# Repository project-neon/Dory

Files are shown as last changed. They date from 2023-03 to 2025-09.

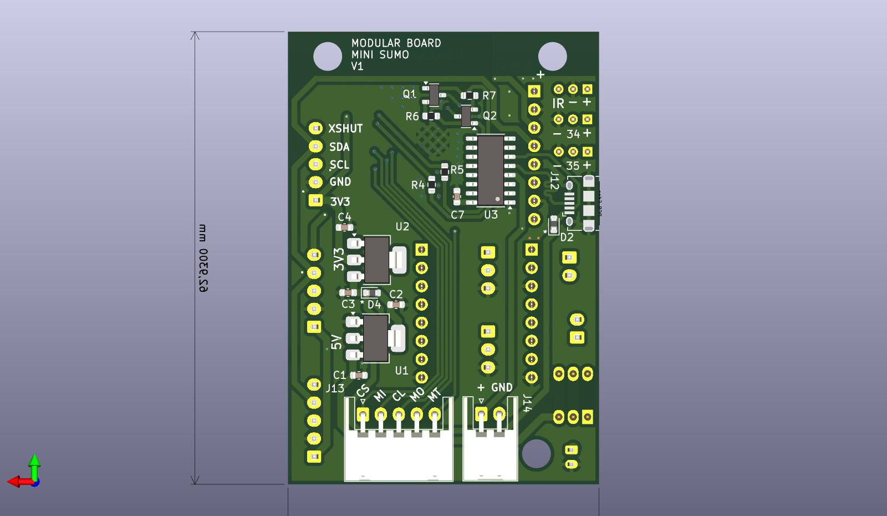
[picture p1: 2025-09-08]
Electronics/Arquivos do projeto/Sumo_Geral_Modular B.jpg

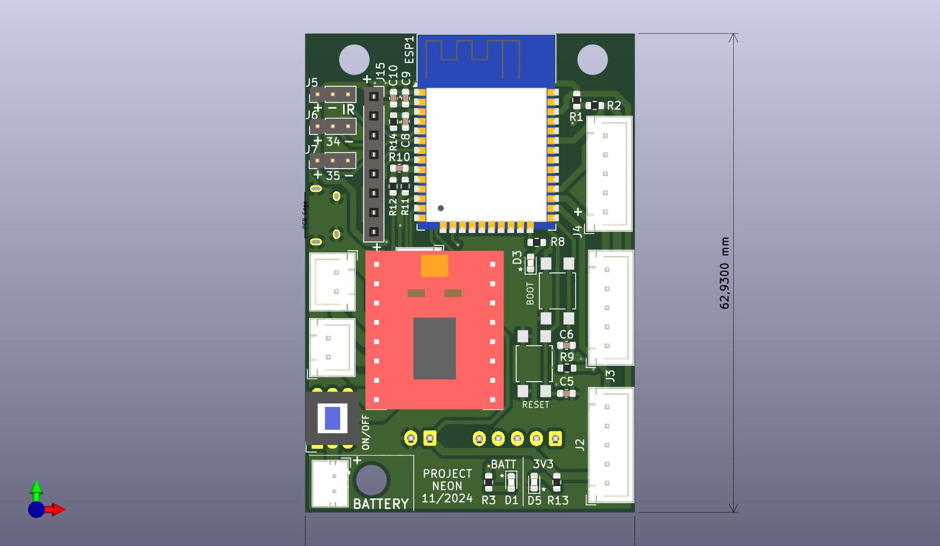
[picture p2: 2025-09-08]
Electronics/Arquivos do projeto/Sumo_Geral_Modular F.jpg

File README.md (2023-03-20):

# Dory
3rd Sumo Robot for Project Neon. After Zumo and Nemo, comes Dory.

Repositório de desenvolvimento para a Dory em 2022.

Usamos o fluxo de trabalho apresentado [aqui pelo Gamen](https://github.com/project-neon/codestyleguide/blob/master/git.md). Também está apresentado no [github flow](https://docs.github.com/pt/get-started/quickstart/github-flow). O resumo seria este:

## Arquivos

  Neste repositório temos os principais arquivos que usamos para os 3 capítulos, Eletrônica, Mecânica e Software. Segue abaixo uma lista do que temos em cada uma das pastas:

  ### Electronics
    Na parte eletrônica, utilizamos o programa Kicad que é open source e permite a criação e edição de PCBs.
    Caso queira editar ou vizualizar o projeto, clone o diretório "Eletronics", pois nele está contido o esquemático 
    no formato PDF e sch,  a PCB no formato pcb e os arquivos pro e plr próprios do Kicad.
    
  ### Mechanics
    Na pasta da mecânica, há arquivos no formato step e stl para que possam ser utilizados para visualização 
    e manufatura 3D, juntamente com os arquivos pdf dos desenhos técnicos para melhor compreensão do projeto
    
  ### Software
    Nesta pasta deixamos todos os arquivos que formam o código do robô. Então .ino e .h são os principais arquivos.
    Usamos os .h's para segmentar o código e não ser um único bloco enorme, dividindo eles de acordo com sua funcionalidade.
    O .ino é onde fica a base de todo o código, como o setup() e o loop(). Temos os códigos de testes e o código autonomous
    que usamos durante as lutas oficiais.

## Fluxo Git
- Quando for acrescentar uma feature (um comportamento novo para o robô), crie uma brancha chamada `feat/nome-da-feature`
- Quando for corrir algum bug no código, crie uma brancha chamada `fix/nome-do-fix`
- Quando for adicionar novos arquivos na mecância ou eletrônica, crie uma brancha chamada `update/eletronics-<data>` ou `update/mechanis-<data>`, exemplo: `update/eletronics-01-04-2023`
- A partir da main: `git checkout -b nome-da-branch`, ex: `git checkout -b feat/novos-testes`

## Na hora de fazer o commit
- Nomeie o seu commit primeiro dizendo o que foi feito, ex: `fix: `, `feat: ` ou `update: `
- Você pode adicionar no assunto (comentário) ou na mensagem do commit também onde que a mudança foi feita.
- `git push`

Para saber mais de commits, você pode acessar esse [link](https://www.freecodecamp.org/news/how-to-write-better-git-commit-messages/)

## Na hora de fazer o merge
- Depois de subir o commit, crie um PR (Pull Request) e peça pro resto do pessoal da equipe dar uma conferida antes de ser aprovado



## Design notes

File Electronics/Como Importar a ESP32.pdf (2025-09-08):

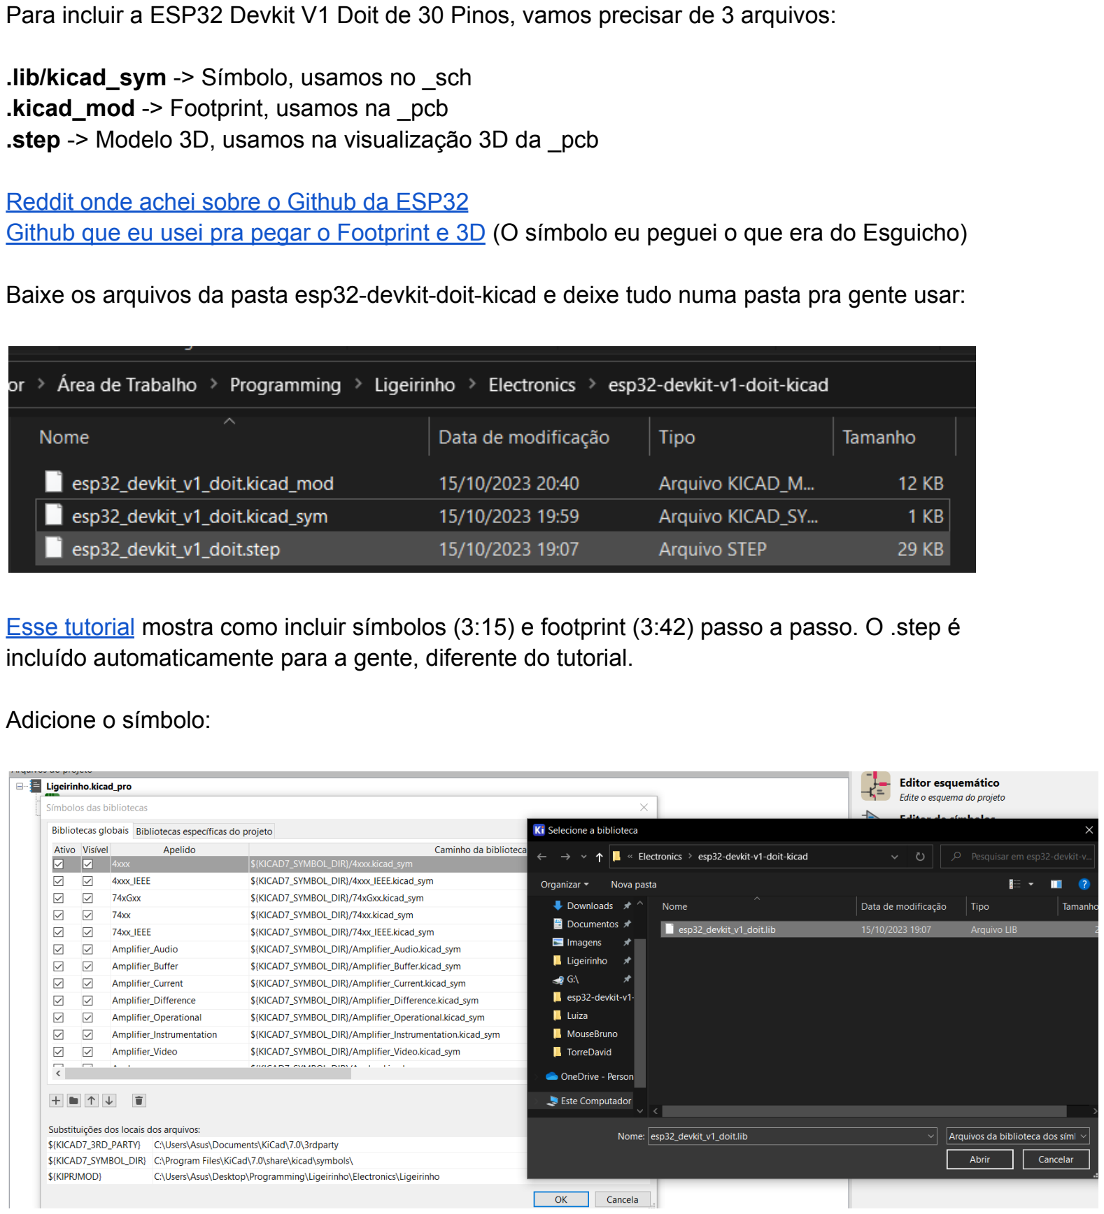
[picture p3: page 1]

Para incluir a ESP32 Devkit V1 Doit de 30 Pinos, vamos precisar de 3 arquivos:

.lib/kicad_sym -> Símbolo, usamos no _sch
.kicad_mod -> Footprint, usamos na _pcb
.step -> Modelo 3D, usamos na visualização 3D da _pcb

Reddit onde achei sobre o Github da ESP32 (https://www.reddit.com/r/esp32/comments/hufwwl/looking_for_kicad_symbolfootprint_for_esp_doit/)
Github que eu usei pra pegar o Footprint e 3D (https://gitlab.com/VictorLamoine/kicad/-/tree/master?ref_type=heads) (O símbolo eu peguei o que era do Esguicho)

Baixe os arquivos da pasta esp32-devkit-doit-kicad e deixe tudo numa pasta pra gente usar:

Esse tutorial (https://www.youtube.com/watch?v=W9cLnIjvybo&ab_channel=PlumPot) mostra como incluir símbolos (3:15) e footprint (3:42) passo a passo. O .step é incluído automaticamente para a gente, diferente do tutorial.

Adicione o símbolo:

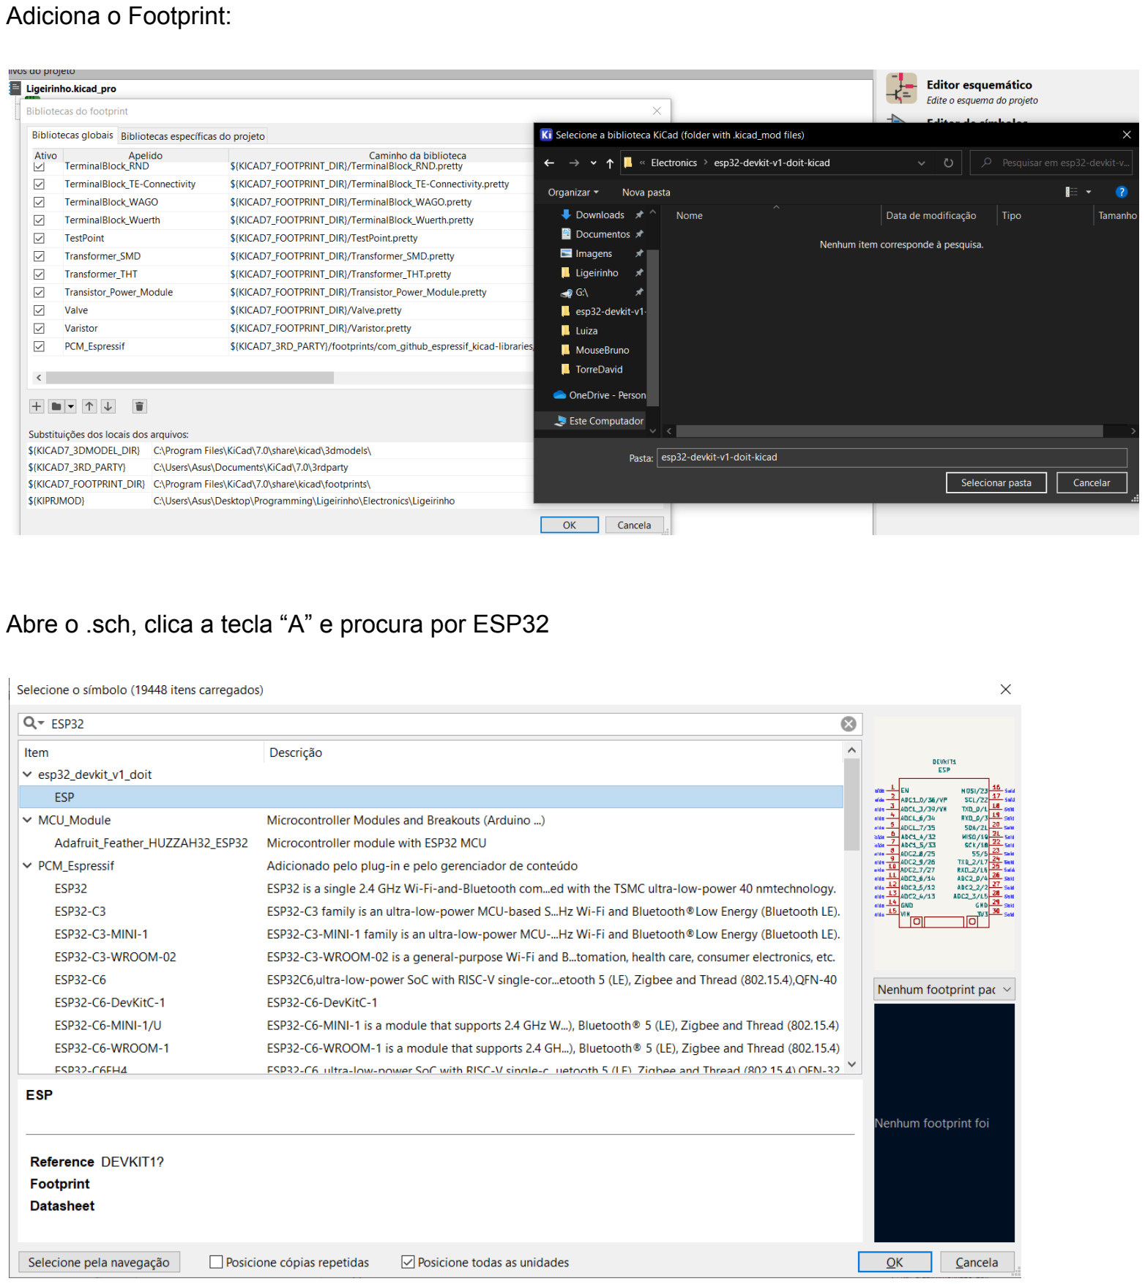
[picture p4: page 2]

Adiciona o Footprint:

Abre o .sch, clica a tecla “A” e procura por ESP32

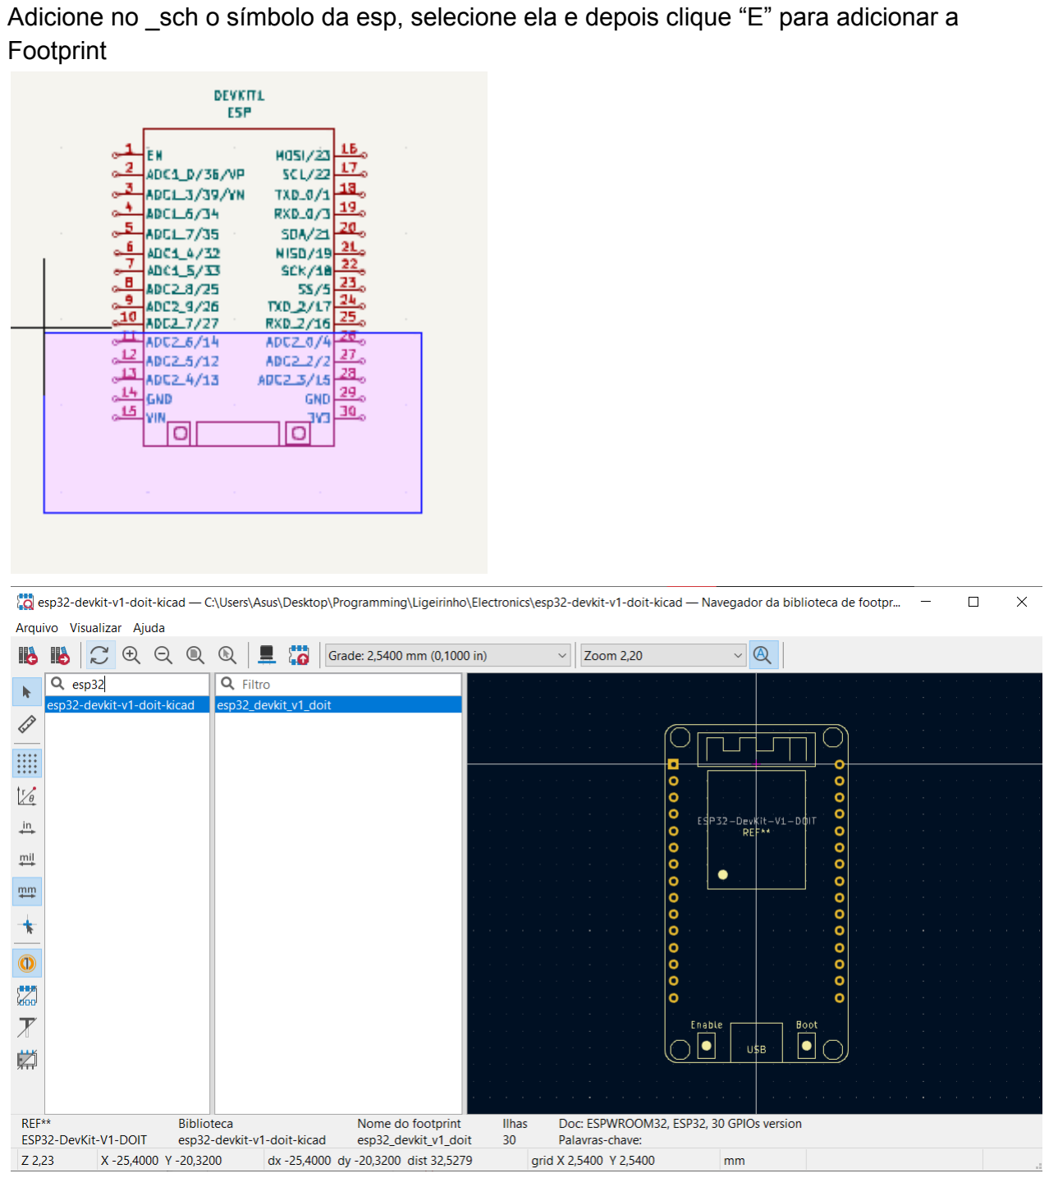
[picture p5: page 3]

A

dicio

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
p, s

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
cliq

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
dicio

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
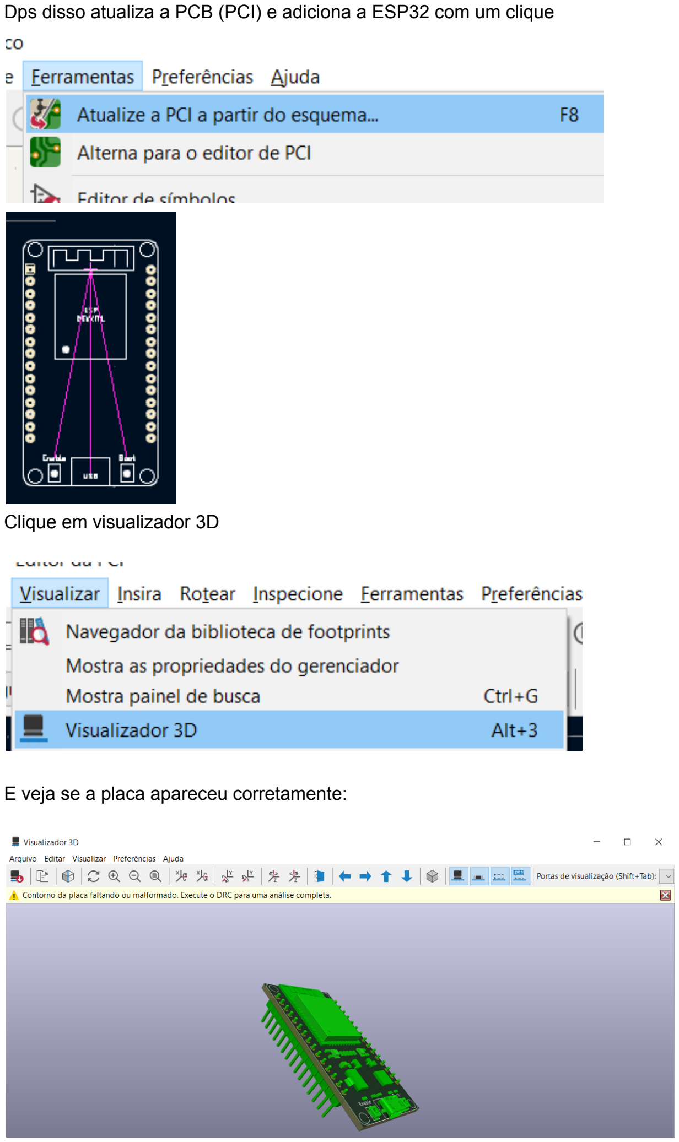
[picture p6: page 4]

Dps disso atualiza a PCB (PCI) e adiciona a ESP32 com um clique

Clique em visualizador 3D

E veja se a placa apareceu corretamente:

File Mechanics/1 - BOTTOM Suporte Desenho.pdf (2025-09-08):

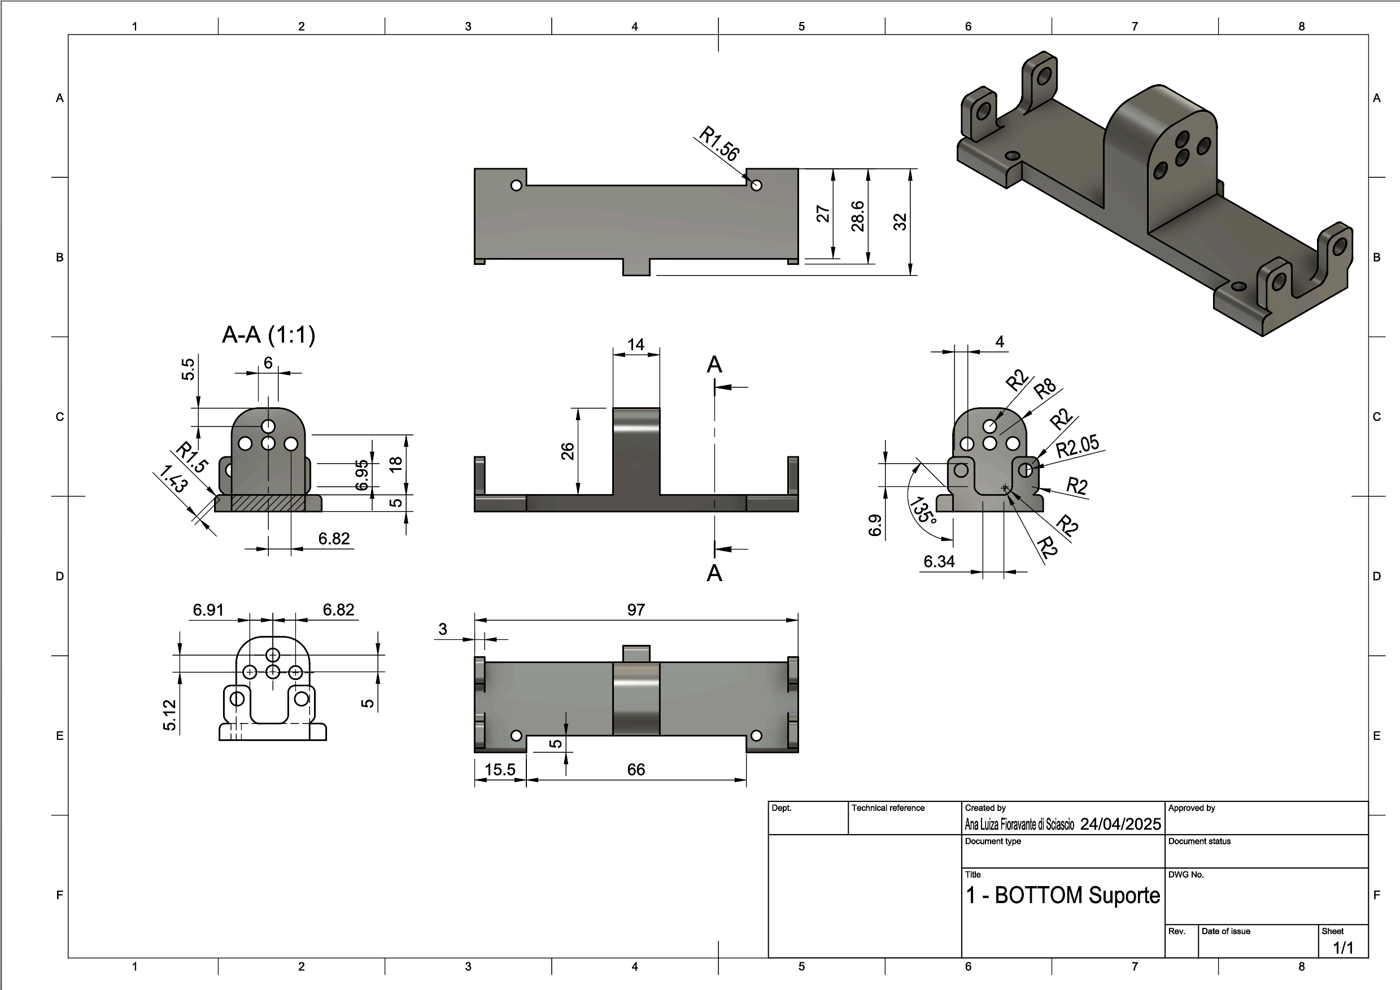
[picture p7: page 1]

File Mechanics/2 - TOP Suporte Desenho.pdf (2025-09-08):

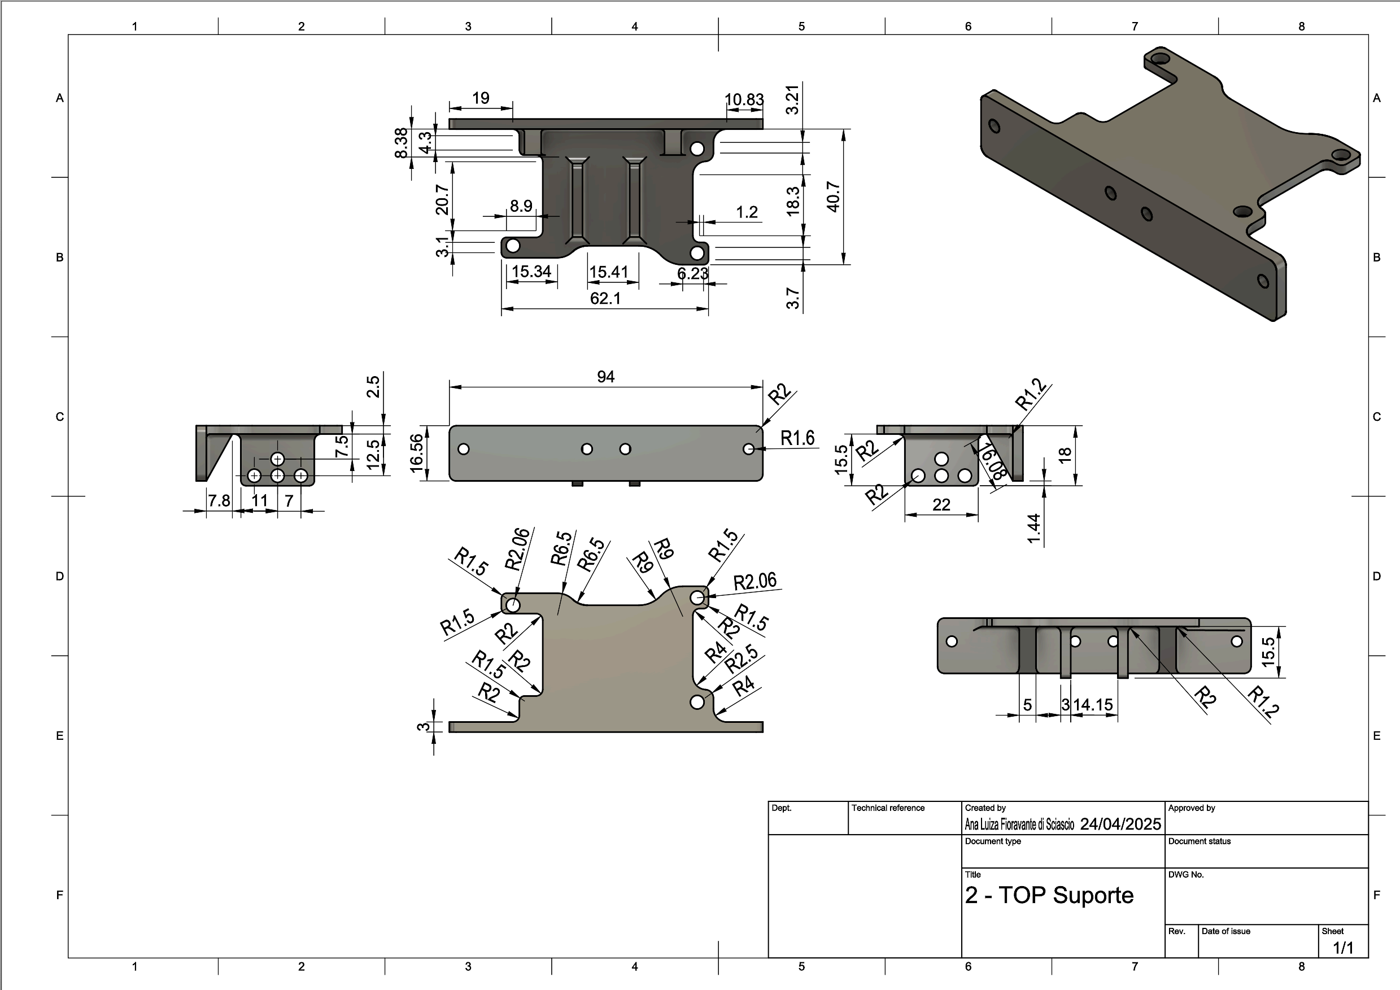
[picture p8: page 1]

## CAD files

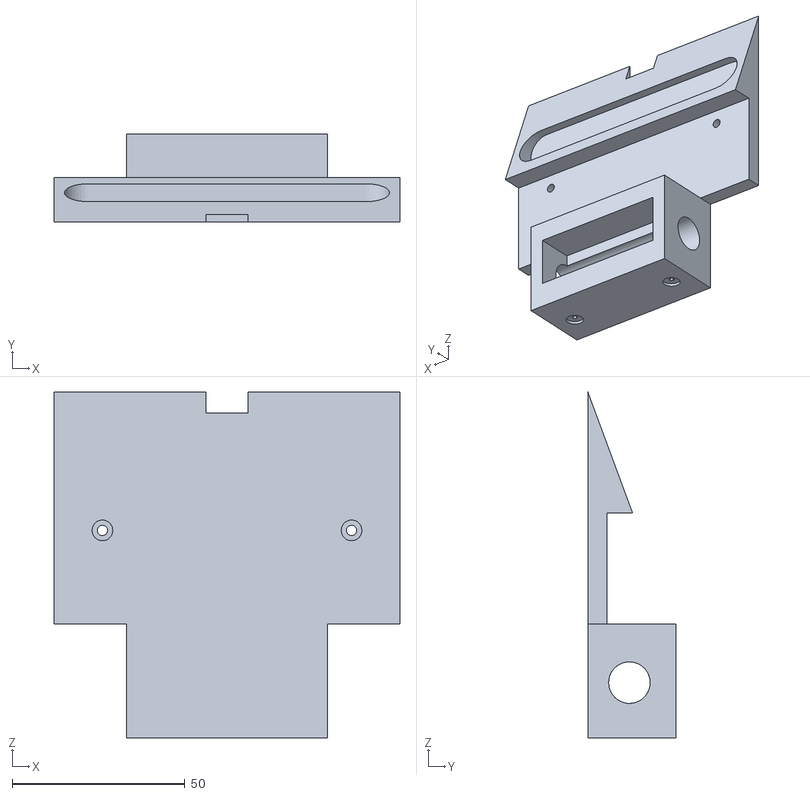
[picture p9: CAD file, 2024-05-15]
Mechanics/Dory_Main_Body Atualizado v5.stl
100.0 x 25.5 x 100.0

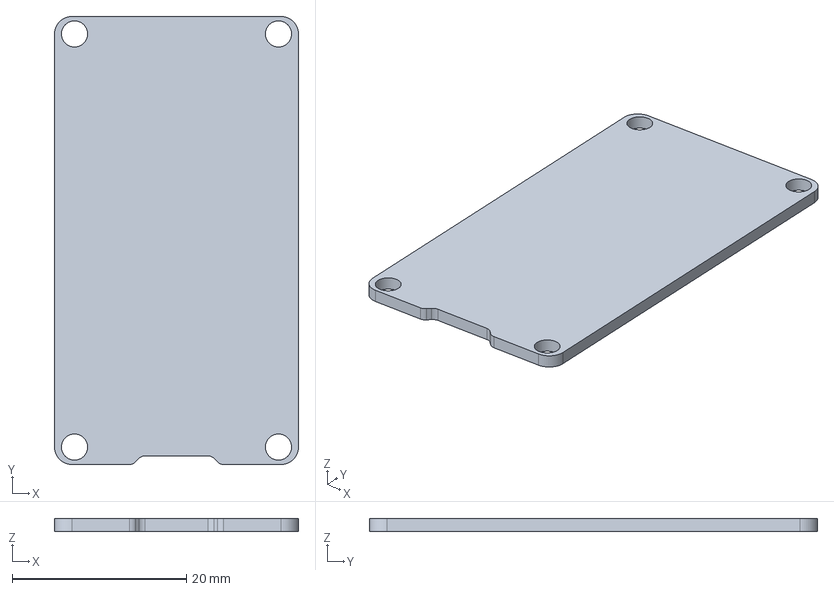
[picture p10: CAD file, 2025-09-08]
Electronics/esp32_devkit_v1_doit/esp32_devkit_v1_doit.step
28.0 x 51.4 x 1.50 mm

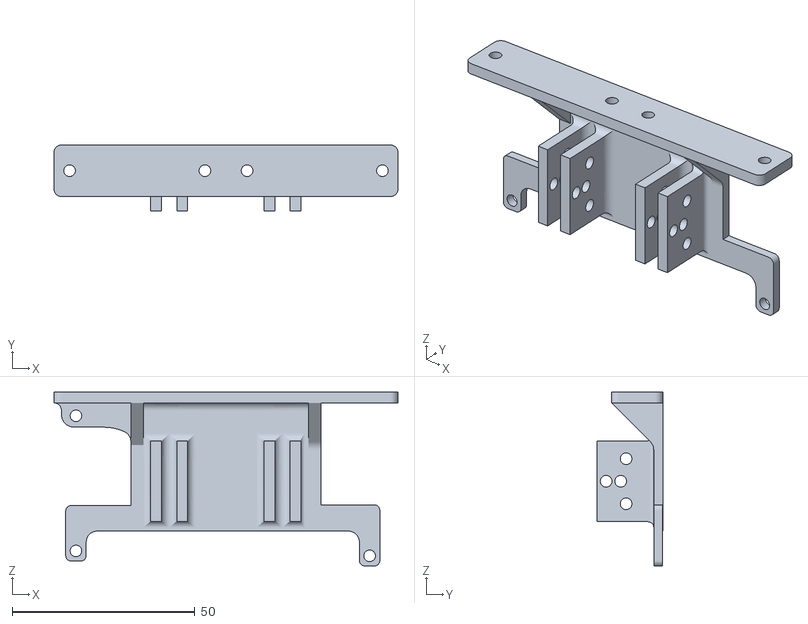
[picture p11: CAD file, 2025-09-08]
Mechanics/TOP-Suporte-Dory.stl
94.0 x 18.0 x 47.5

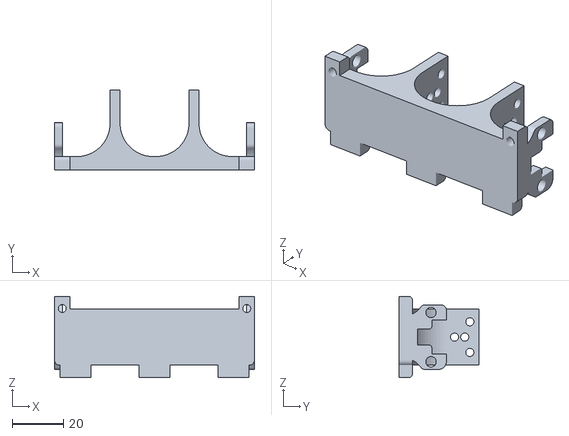
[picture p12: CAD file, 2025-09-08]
Mechanics/BOTTOM-Suporte-Dory.stl
78.3 x 31.2 x 31.9

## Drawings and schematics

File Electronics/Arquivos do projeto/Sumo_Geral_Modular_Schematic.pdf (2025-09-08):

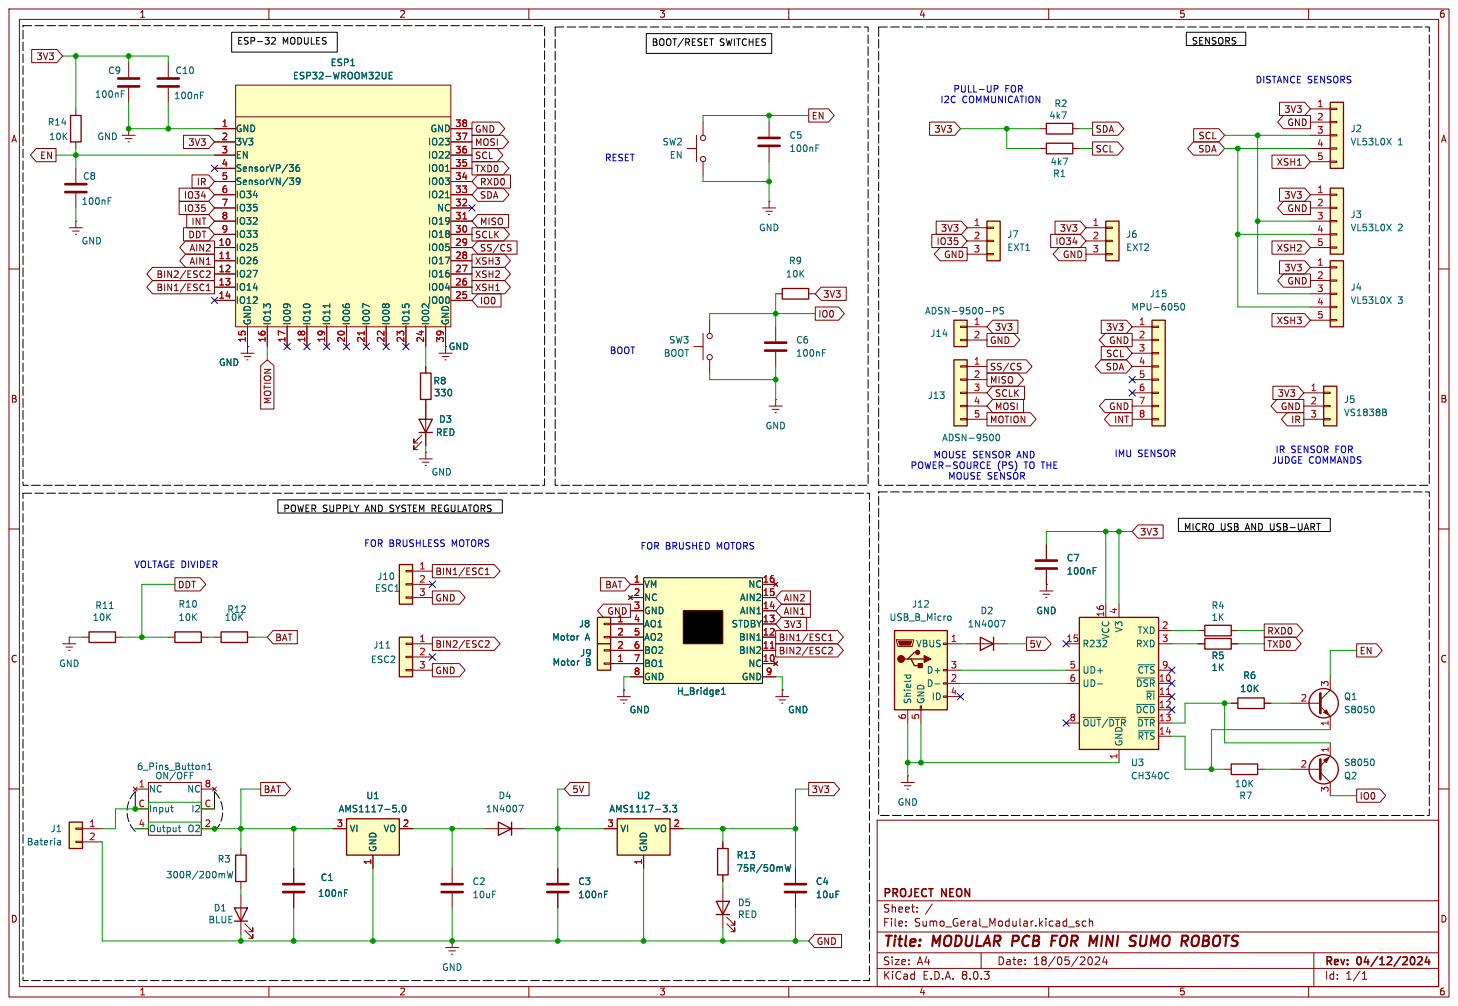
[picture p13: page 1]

DISTANCE SENSORS
I2C COMMUNICATION MOUSE SENSOR AND

POWER-SOURCE (PS) TO THE MOUSE SENSOR

1 VO 2 VI 3 U2 AMS1117-3.3 GND GND

1 ~{DSR} 10 ~{RI} 11 ~{DCD} 12 ~{DTR} 13 ~{RTS} 14 R232 15 VCC 16 TXD 2 RXD 3 V3

4 UD+ 5 UD- 6 ~{OUT}/~{DTR} 8 ~{CTS}9 U3 CH340C

Id: 1/1 Title: MODULAR PCB FOR MINI SUMO ROBOTS

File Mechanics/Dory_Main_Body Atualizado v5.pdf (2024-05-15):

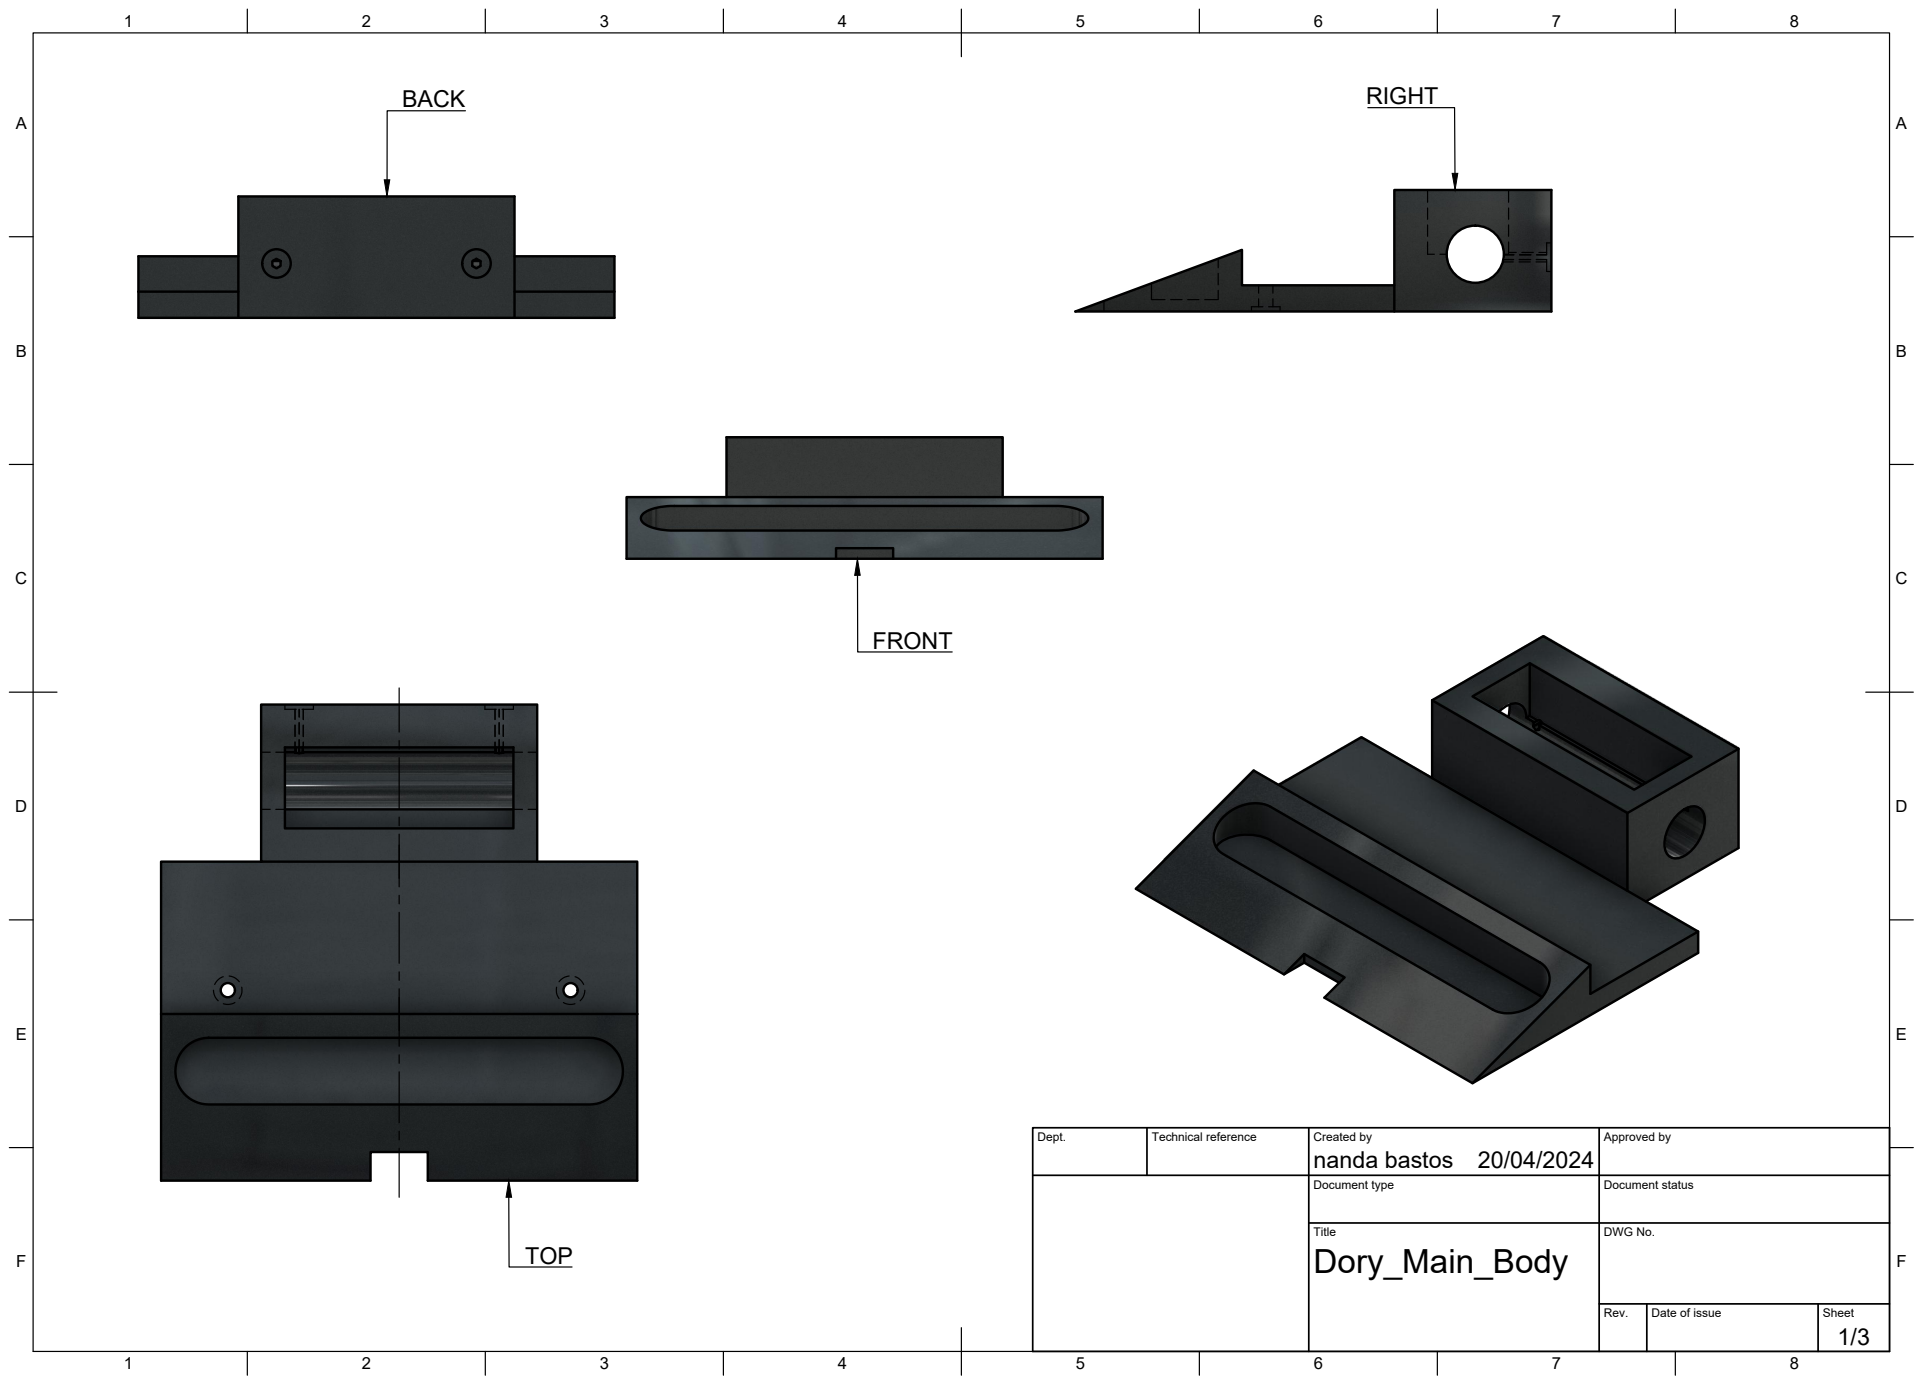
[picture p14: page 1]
Title; DWG No.; Rev.; Date of issue; Sheet

Dept. | Technical reference | Created by nanda bastos 20/04/2024 | Approved by

Document type | Document status

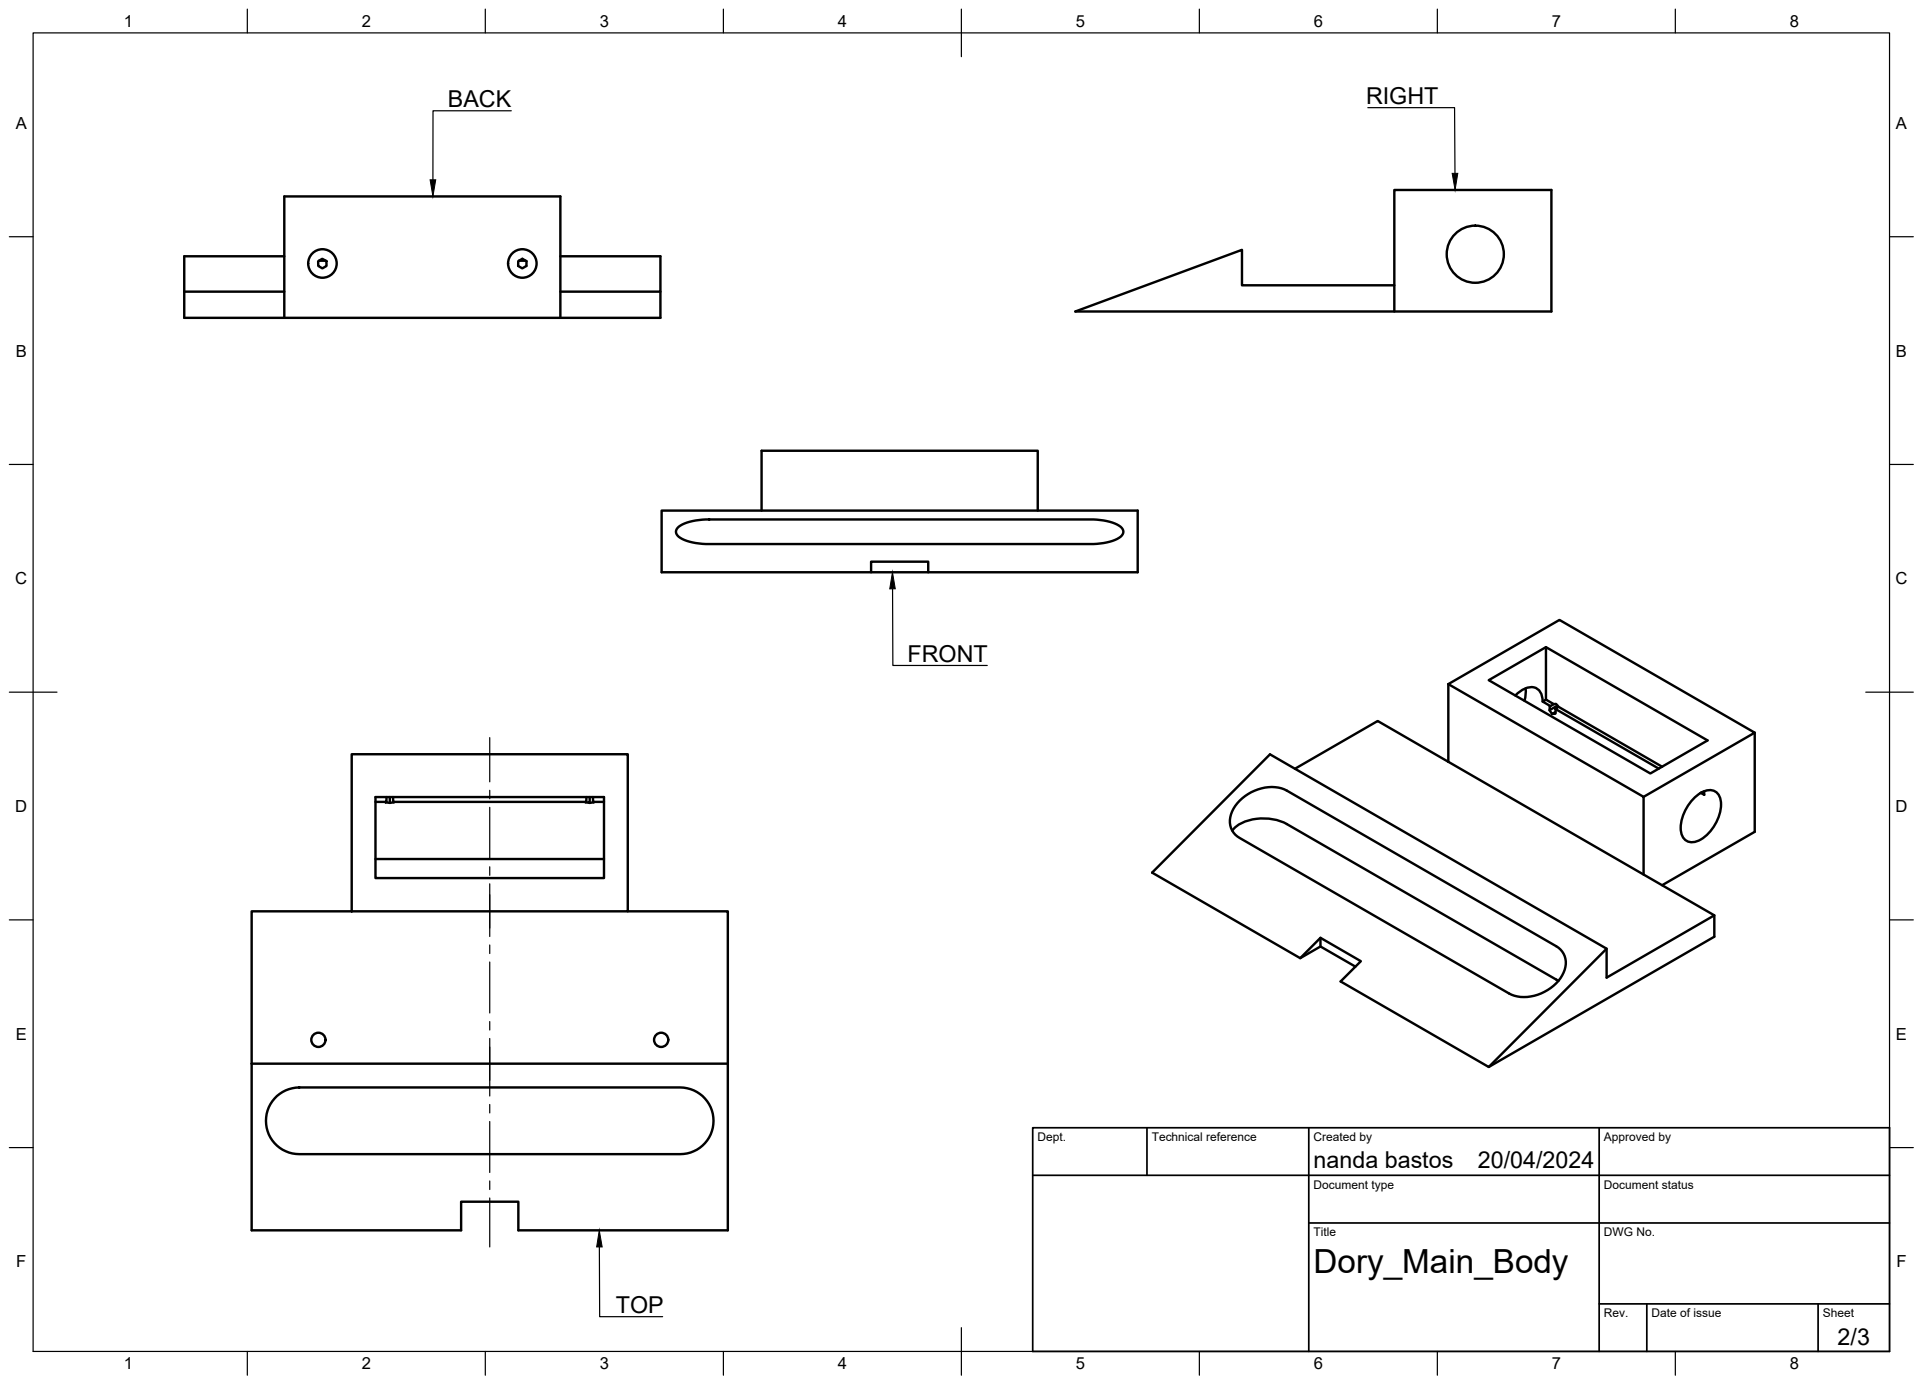
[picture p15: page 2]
Title; DWG No.

Dept. | Technical reference | Created by nanda bastos 20/04/2024 | Approved by

Document type | Document status

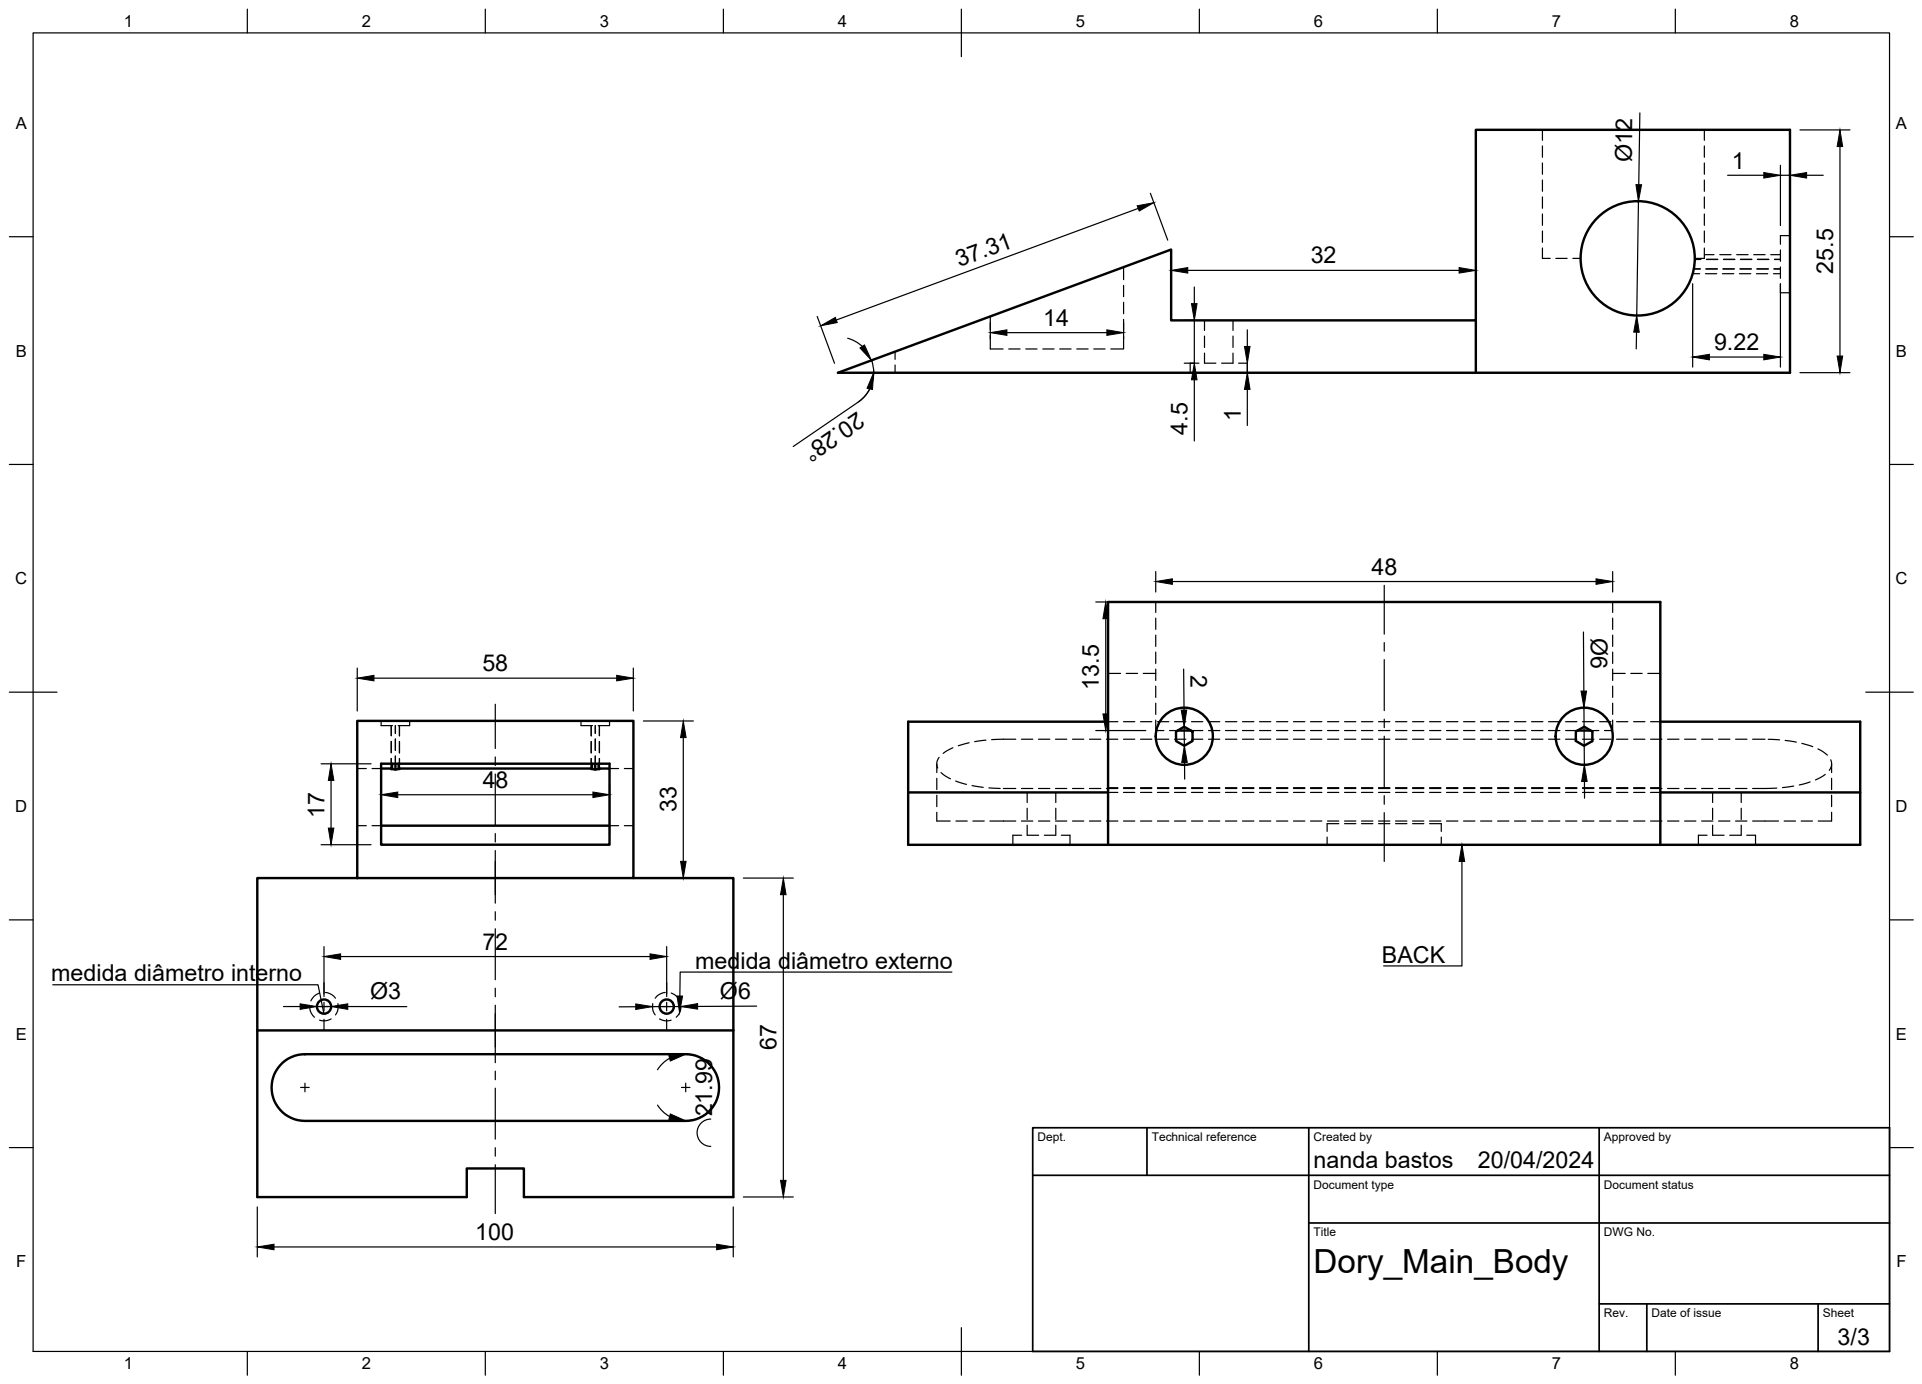
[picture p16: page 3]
Title; DWG No.

medida diâmetro externo medida diâmetro interno

Dept. | Technical reference | Created by nanda bastos 20/04/2024 | Approved by

Document type | Document status

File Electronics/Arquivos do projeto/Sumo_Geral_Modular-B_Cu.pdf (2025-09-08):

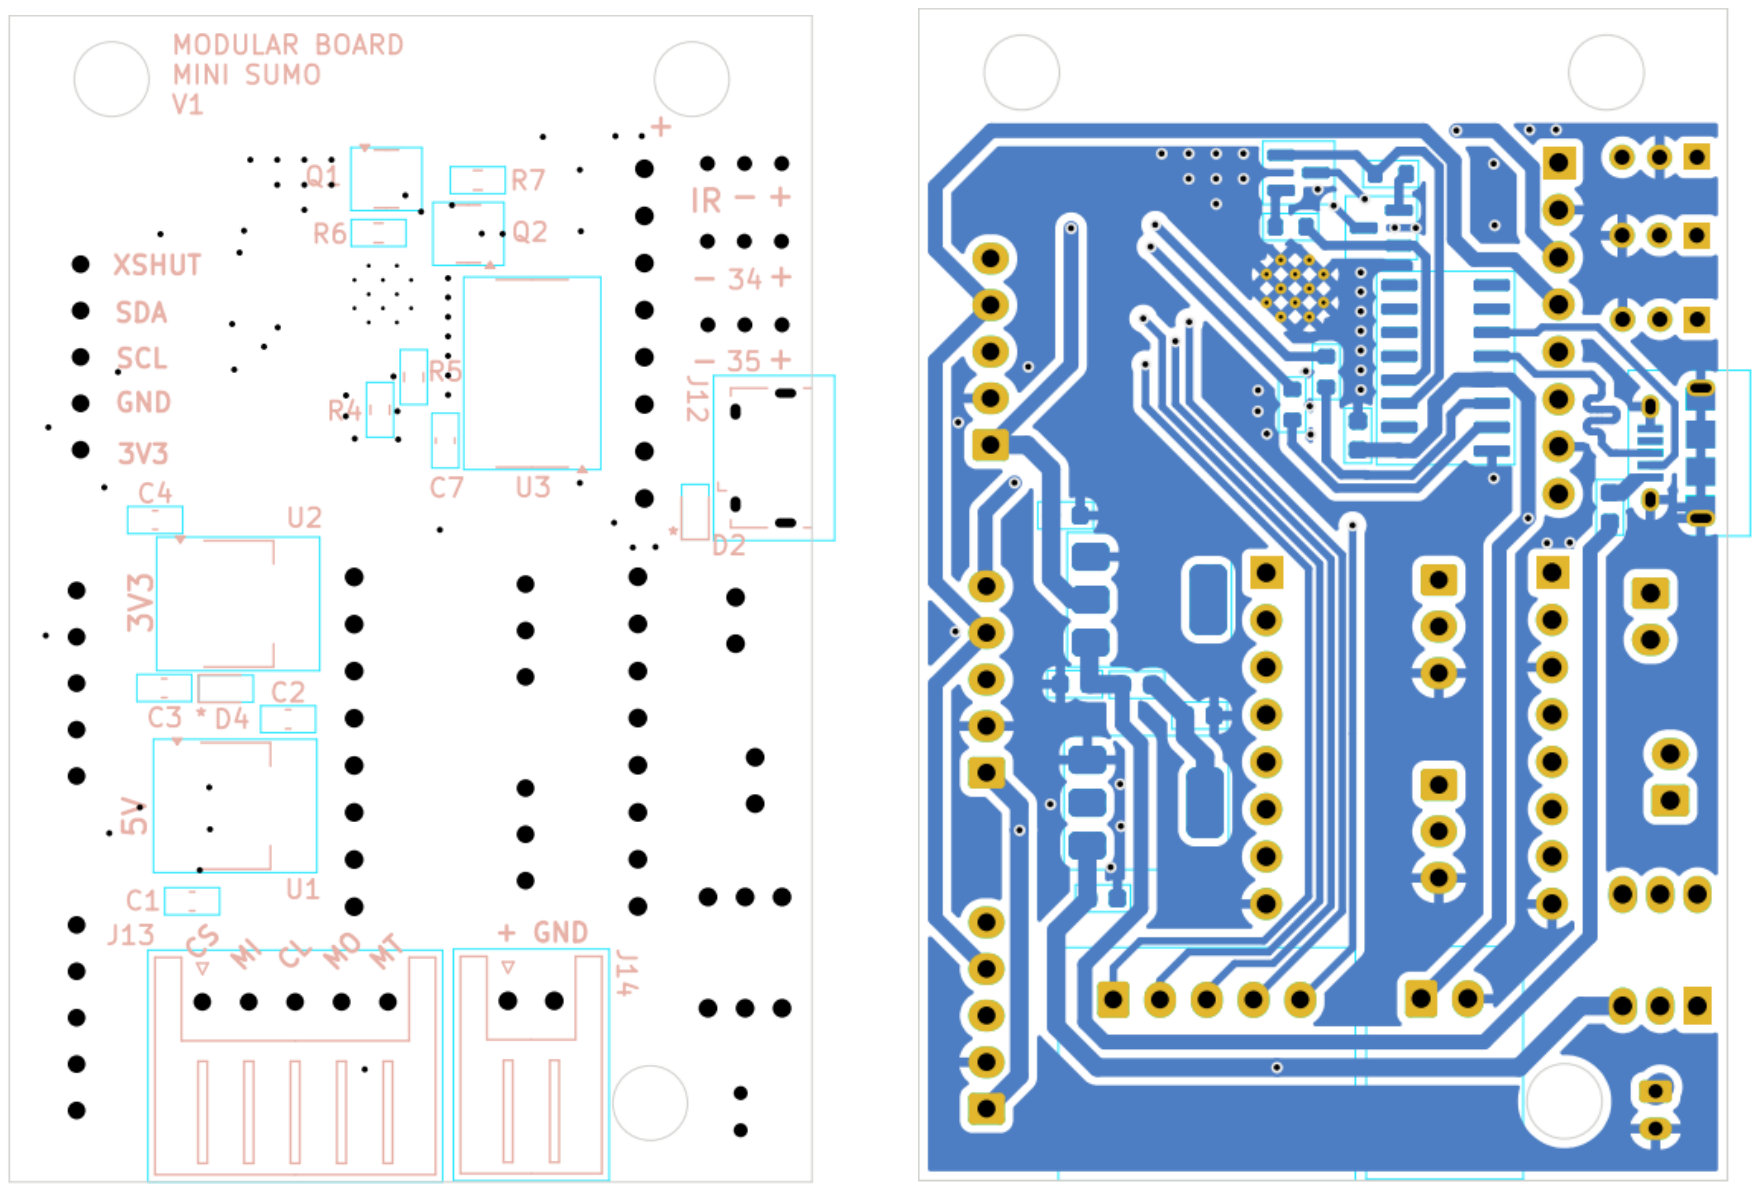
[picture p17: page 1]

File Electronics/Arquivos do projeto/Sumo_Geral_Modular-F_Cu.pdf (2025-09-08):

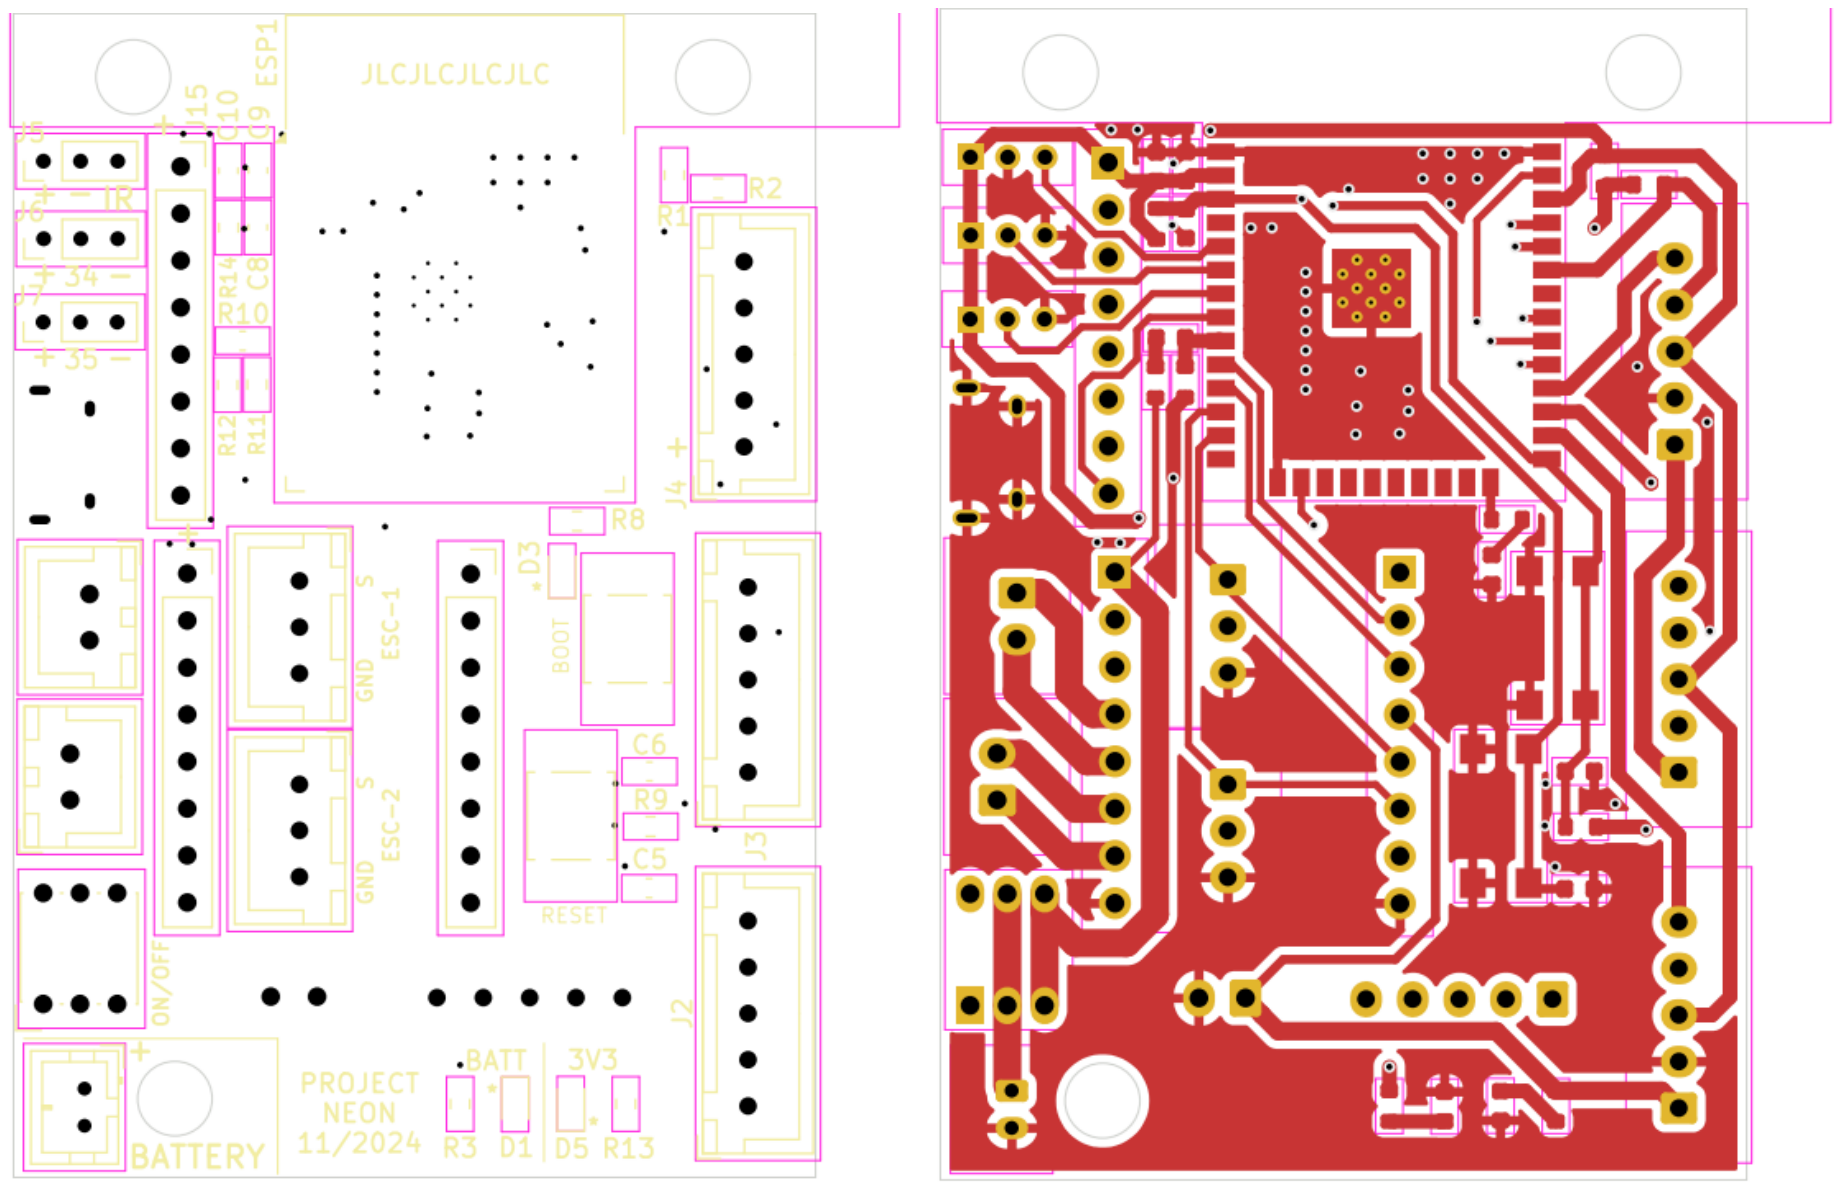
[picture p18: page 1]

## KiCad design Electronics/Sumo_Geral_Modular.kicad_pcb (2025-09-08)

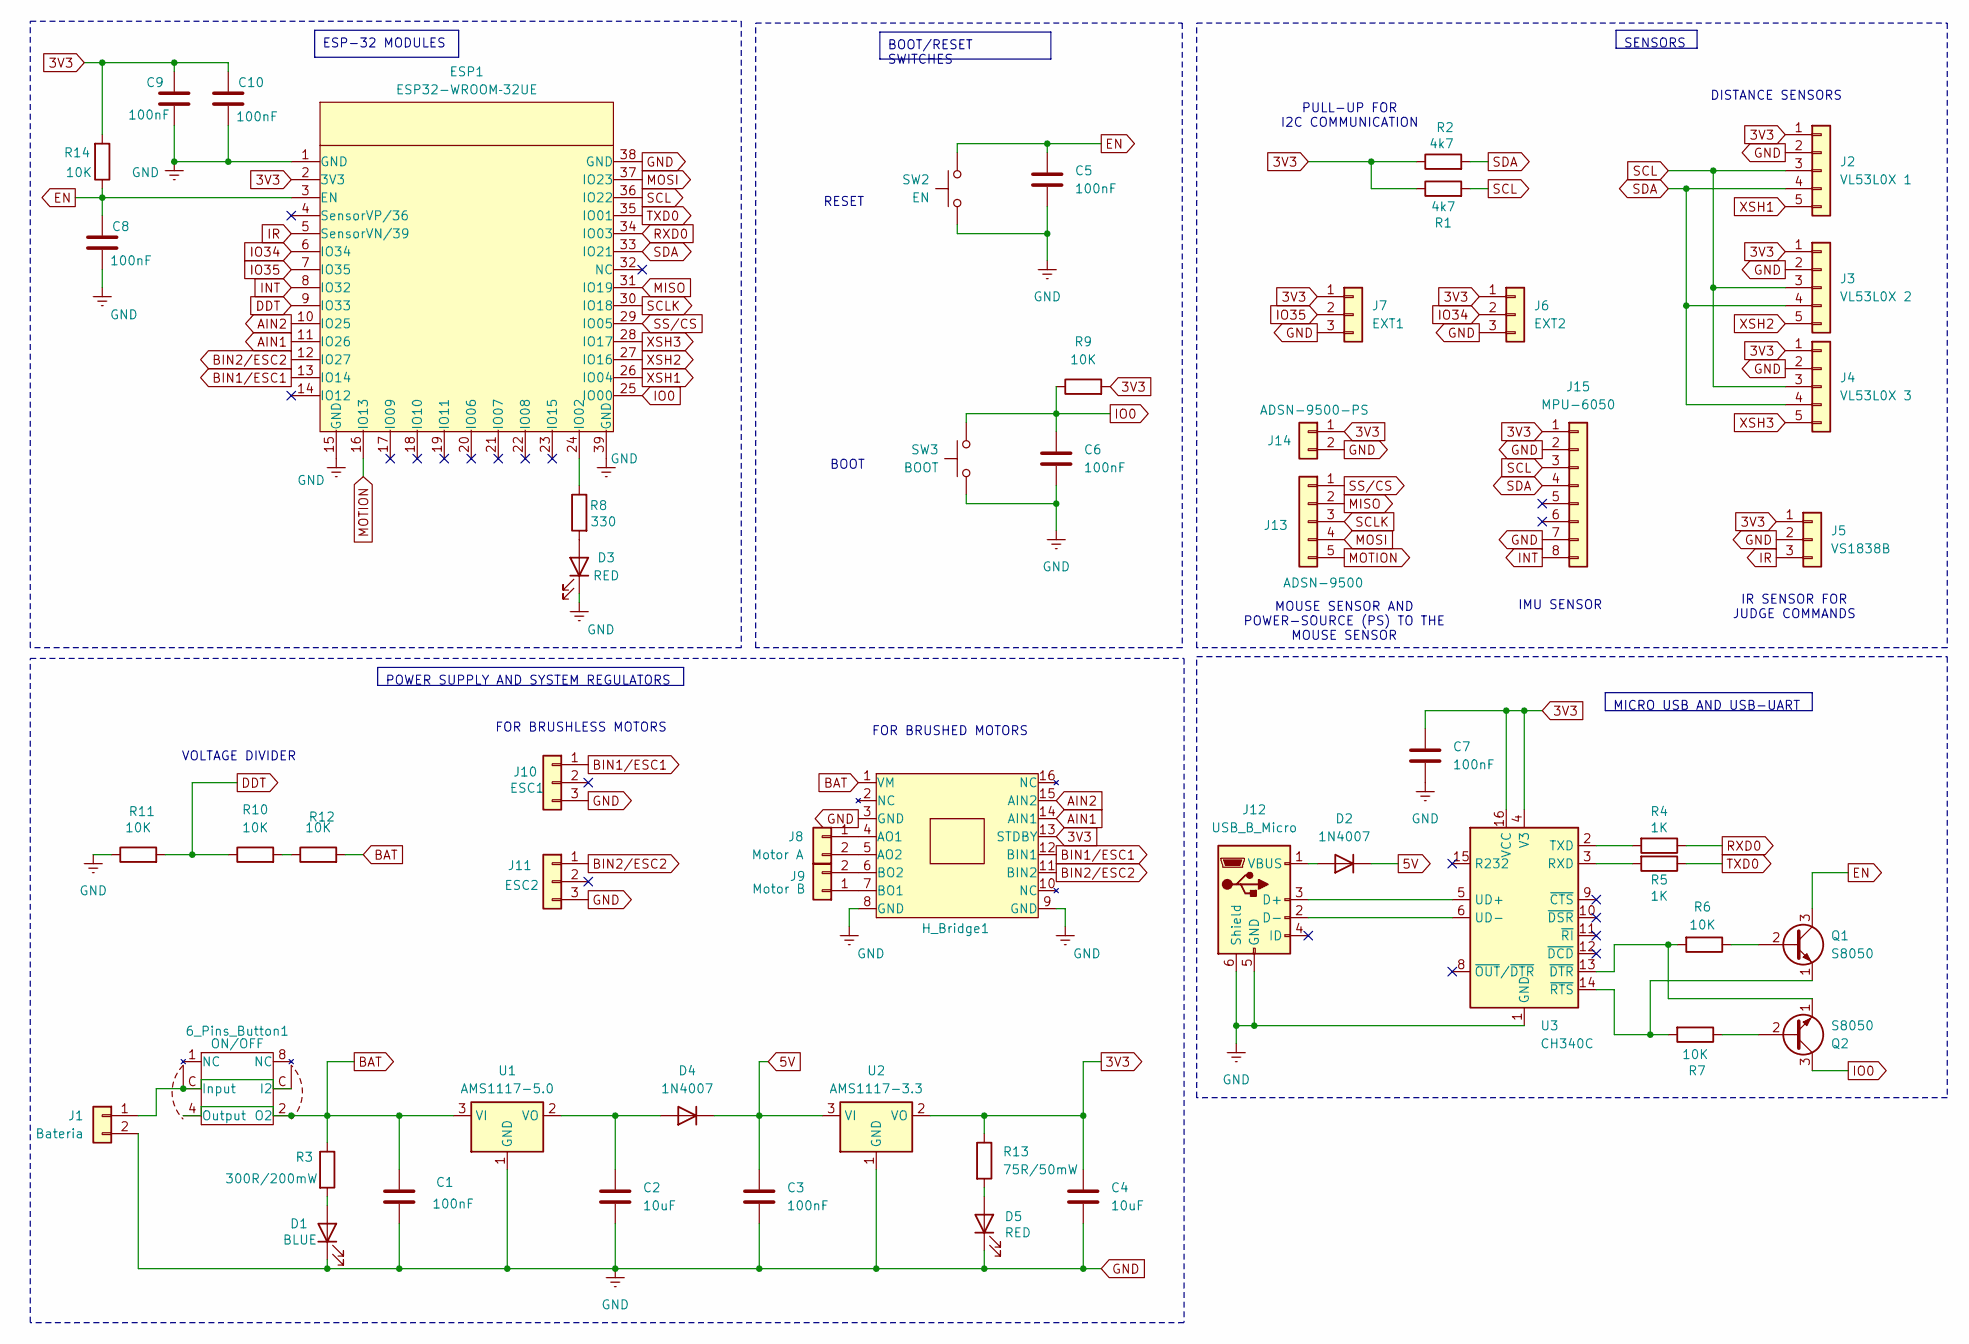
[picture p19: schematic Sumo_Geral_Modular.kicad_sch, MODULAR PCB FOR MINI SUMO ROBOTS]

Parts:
6_Pins_Button1: ON/OFF; Push_Button_6_pins
C1, C3, C5, C6, C7, C8, C9, C10: 100nF; C_0603_1608Metric
C2, C4: 10uF; C_0603_1608Metric
D1: BLUE; LED_0603_1608Metric
D2, D4: 1N4007; D_0603_1608Metric
D3, D5: RED; LED_0603_1608Metric
ESP1: ESP32-WROOM­32UE; ESP32-WROOM-32
H_Bridge1: H_Bridge_with_headers
J1: Bateria; JST_PH_B2B-PH-K_1x02_P2.00mm_Vertical
J2: VL53L0X 1; JST_XH_B5B-XH-A_1x05_P2.50mm_Vertical
J3: VL53L0X 2; JST_XH_B5B-XH-A_1x05_P2.50mm_Vertical
J4: VL53L0X 3; JST_XH_B5B-XH-A_1x05_P2.50mm_Vertical
J5: VS1838B; PinHeader_1x03_P2.00mm_Vertical
J6: EXT2; PinHeader_1x03_P2.00mm_Vertical
J7: EXT1; PinHeader_1x03_P2.00mm_Vertical
J8: Motor A; JST_XH_B2B-XH-A_1x02_P2.50mm_Vertical
J9: Motor B; JST_XH_B2B-XH-A_1x02_P2.50mm_Vertical
J10: ESC1; JST_XH_B3B-XH-A_1x03_P2.50mm_Vertical
J11: ESC2; JST_XH_B3B-XH-A_1x03_P2.50mm_Vertical
J12: USB_B_Micro; USB_Micro-B_Amphenol_10118194_Horizontal
J13: ADSN-9500; JST_XH_S5B-XH-A_1x05_P2.50mm_Horizontal
J14: ADSN-9500-PS; JST_XH_S2B-XH-A_1x02_P2.50mm_Horizontal
J15: MPU-6050; PinSocket_1x08_P2.54mm_Vertical
Q1, Q2: S8050; SOT-23
R1, R2: 4k7; R_0603_1608Metric
R3: 300R/200mW; R_0603_1608Metric
R4, R5: 1K; R_0603_1608Metric
R6, R7, R9, R11, R12, R14: 10K; R_0603_1608Metric
R8: 330; R_0603_1608Metric
R10: 10K; C_0603_1608Metric
R13: 75R/50mW; R_0603_1608Metric
SW2: EN; SW_SPST_TL3305C
SW3: BOOT; SW_SPST_TL3305C
U1: AMS1117-5.0; SOT-223-3_TabPin2
U2: AMS1117-3.3; SOT-223-3_TabPin2
U3: CH340C; SOIC-16_3.9x9.9mm_P1.27mm

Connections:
3V3: C4.1, C7.1, C9.1, C10.1, ESP1.2 (3V3), H_Bridge1.13 (STDBY), J2.1, J3.1, J4.1, J5.1, J6.1, J7.1, J14.1, J15.1, R1.1, R2.1, R9.2, R13.1, R14.2, U2.2 (VO), U3.4 (V3), U3.16 (VCC)
5V: C3.1, D2.1 (K), D4.1 (K), U2.3 (VI)
AIN1: ESP1.11 (IO26), H_Bridge1.14 (AIN1)
AIN2: ESP1.10 (IO25), H_Bridge1.15 (AIN2)
BAT: 6_Pins_Button1.2 (O2), 6_Pins_Button1.4 (Output), C1.1, H_Bridge1.1 (VM), R3.1, R12.2, U1.3 (VI)
BIN1/ESC1: ESP1.13 (IO14), H_Bridge1.12 (BIN1), J10.1
BIN2/ESC2: ESP1.12 (IO27), H_Bridge1.11 (BIN2), J11.1
DDT: ESP1.9 (IO33), R10.1, R11.2
EN: C5.2, C8.1, ESP1.3 (EN), Q1.3 (C), R14.1, SW2.1
GND: C1.2, C2.2, C3.2, C4.2, C5.1, C6.2, C7.2, C8.2, C9.2, C10.2, D1.1 (K), D3.1 (K), D5.1 (K), ESP1.1 (GND), ESP1.15 (GND), ESP1.38 (GND), ESP1.39 (GND), H_Bridge1.3 (GND), H_Bridge1.8 (GND), H_Bridge1.9 (GND), J1.2, J2.2, J3.2, J4.2, J5.2, J6.3, J7.3, J10.3, J11.3, J12.5 (GND), J12.6 (Shield), J14.2, J15.2, J15.7, R11.1, SW2.2, SW3.2, U1.1 (GND), U2.1 (GND), U3.1 (GND)
INT: ESP1.8 (IO32), J15.8
IO0: C6.1, ESP1.25 (IO00), Q2.3 (C), R9.1, SW3.1
IO34: ESP1.6 (IO34), J6.2
IO35: ESP1.7 (IO35), J7.2
IR: ESP1.5 (SensorVN/39), J5.3
MISO: ESP1.31 (IO19), J13.2
MOSI: ESP1.37 (IO23), J13.4
MOTION: ESP1.16 (IO13), J13.5
unnamed: 6_Pins_Button1.C (I2), J1.1
unnamed: D1.2 (A), R3.2
unnamed: D2.2 (A), J12.1 (VBUS)
unnamed: D3.2 (A), R8.2
unnamed: C2.1, D4.2 (A), U1.2 (VO)
unnamed: D5.2 (A), R13.2
unnamed: ESP1.24 (IO02), R8.1
unnamed: H_Bridge1.4 (AO1), J8.1
unnamed: H_Bridge1.5 (AO2), J8.2
unnamed: H_Bridge1.7 (BO1), J9.1
unnamed: H_Bridge1.6 (BO2), J9.2
unnamed: J12.3 (D+), U3.5 (UD+)
unnamed: J12.2 (D-), U3.6 (UD-)
unnamed: Q1.2 (B), R6.1
unnamed: Q1.1 (E), R7.2, U3.14 (~RTS)
unnamed: Q2.2 (B), R7.1
unnamed: Q2.1 (E), R6.2, U3.13 (~DTR)
unnamed: R10.2, R12.1
unnamed: R5.2, U3.3 (RXD)
unnamed: R4.2, U3.2 (TXD)
RXD0: ESP1.34 (IO03), R4.1
SCL: ESP1.36 (IO22), J2.3, J3.3, J4.3, J15.3, R1.2
SCLK: ESP1.30 (IO18), J13.3
SDA: ESP1.33 (IO21), J2.4, J3.4, J4.4, J15.4, R2.2
SS/CS: ESP1.29 (IO05), J13.1
TXD0: ESP1.35 (IO01), R5.1
XSH1: ESP1.26 (IO04), J2.5
XSH2: ESP1.27 (IO16), J3.5
XSH3: ESP1.28 (IO17), J4.5

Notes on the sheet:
SENSORS
ESP-32 MODULES
BOOT/RESET SWITCHES
MICRO USB AND USB-UART
POWER SUPPLY AND SYSTEM REGULATORS
MOUSE SENSOR AND POWER-SOURCE (PS) TO THE MOUSE SENSOR
FOR BRUSHLESS MOTORS
VOLTAGE DIVIDER
FOR BRUSHED MOTORS
PULL-UP FOR I2C COMMUNICATION
IR SENSOR FOR JUDGE COMMANDS
IMU SENSOR
DISTANCE SENSORS
BOOT
RESET

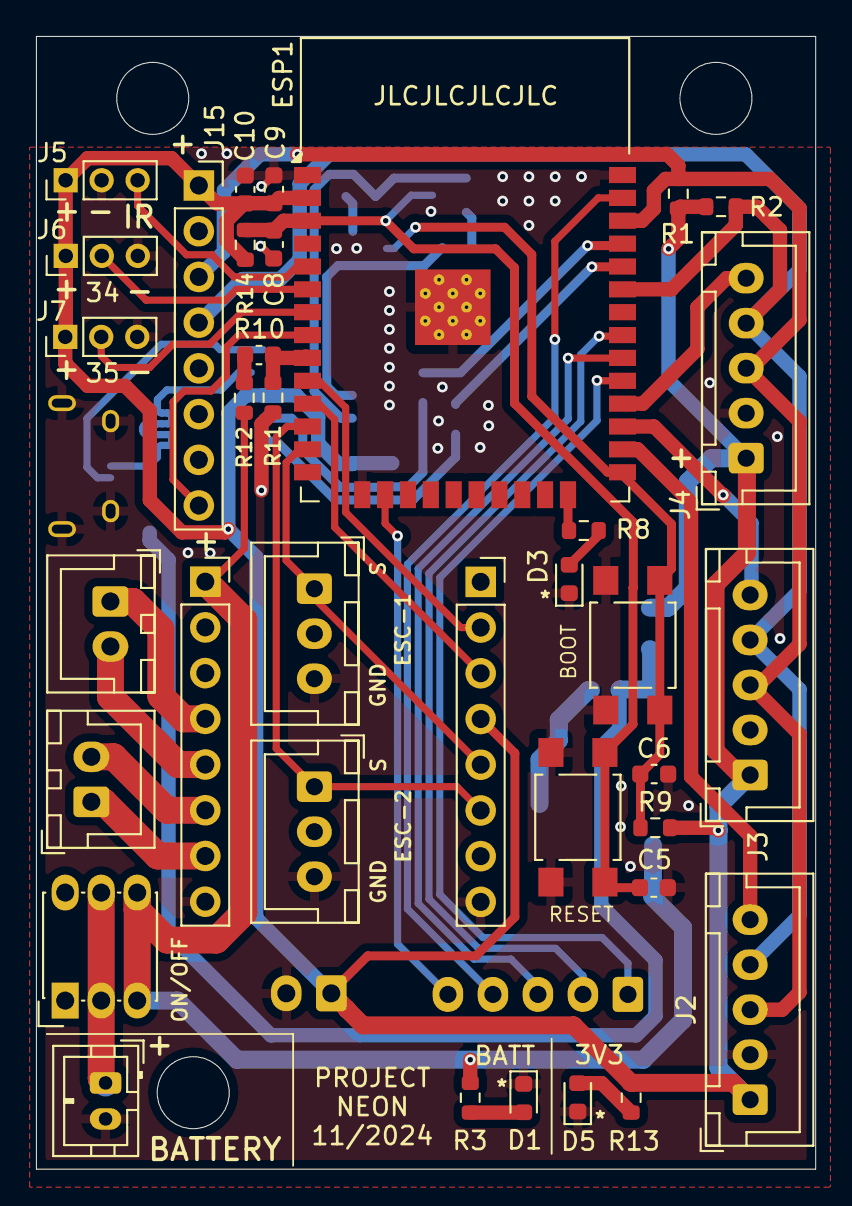
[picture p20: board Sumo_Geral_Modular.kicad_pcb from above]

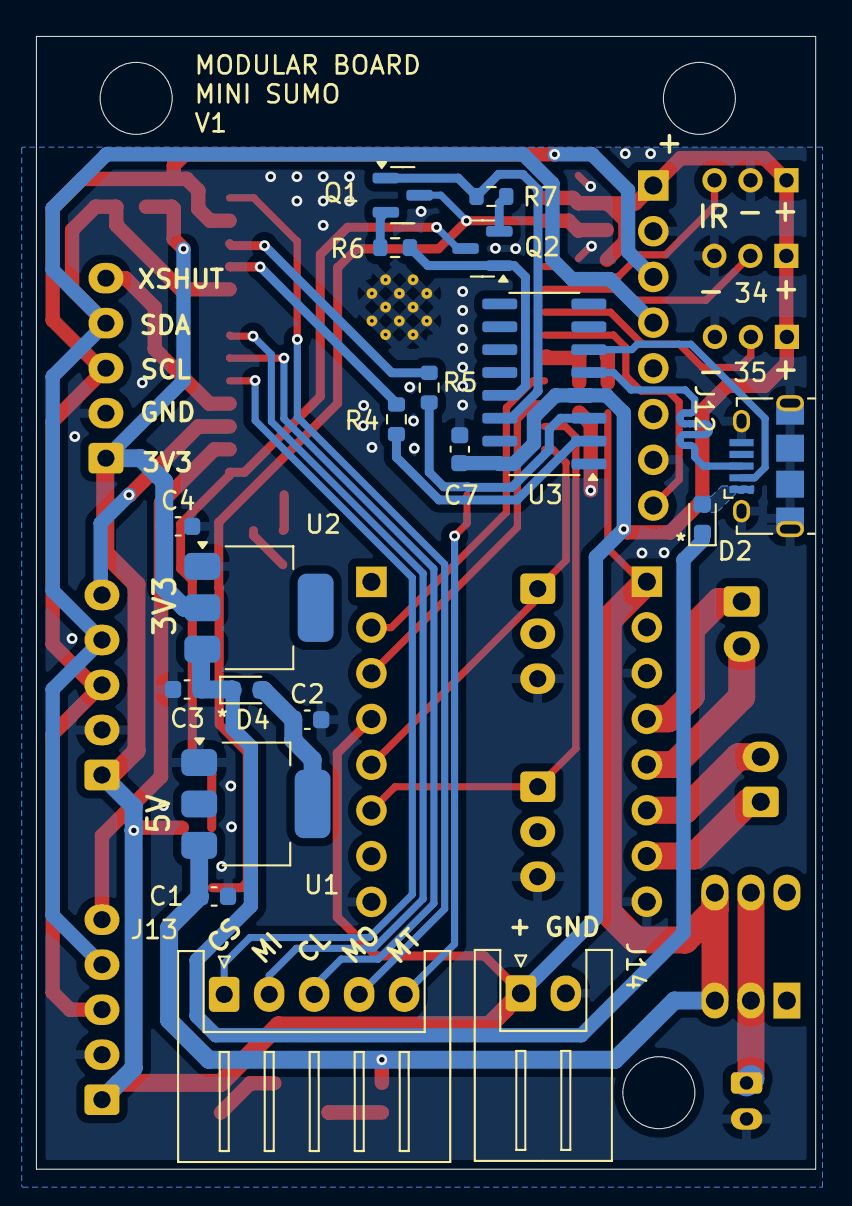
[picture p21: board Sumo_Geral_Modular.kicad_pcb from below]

Board: 2 copper layers, 43.3 x 62.9 mm, 54 parts (19 on the bottom side), 47 nets.

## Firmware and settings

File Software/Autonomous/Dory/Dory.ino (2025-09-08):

// Outros arquivos da dory
#include "Pinout.h"
#include "MotorsHBridgeDRV8833.h"
#include "DistanceSensors.h"
#include "IRJudgeControllerVS1838B.h"

// Declara as variáveis do robô
int enemyLastTimeSeenLeft = 0;  //enemyLastTimeSeenLeft 0: esquerda; enemyLastTimeSeenLeft 1: direita
int velMaxR = 100;
int velMaxL = 97.5;


// Criação da estratégia simples da Dory
void simpleStrategy() {

  if (distanceCenterLeft >= minimumDistanceSharp && distanceCenterRight >= minimumDistanceSharp) {  // Quando o inimigo é percebido à frente
    velMotorL = velMaxL;
    velMotorR = velMaxR;
    Serial.print("ATACANDO \t\t");
  } else if (distanceCenterLeft >= minimumDistanceSharp || distanceCenterRight >= minimumDistanceSharp) {  // Procurando o inimigo
    velMotorL = (distanceCenterLeft >= minimumDistanceSharp) ? velMaxR * 0.7 : velMaxL;                    // Achei na esquerda
    velMotorR = (distanceCenterLeft >= minimumDistanceSharp) ? velMaxR : velMaxL * 0.7;                    // Achei na direita
    enemyLastTimeSeenLeft = (distanceCenterLeft >= minimumDistanceSharp) ? 0 : 1;
    (distanceCenterLeft >= minimumDistanceSharp) ? Serial.print("ESQ \t\t") : Serial.print("DIR \t\t");
  } else {                                                                      // Quando perco o inimigo, duas opções dado a última leitura do sensor:
    velMotorL = (enemyLastTimeSeenLeft == 0) ? -velMaxR * 0.4 : velMaxL * 0.4;  // Gira pra esquerda ou
    velMotorR = (enemyLastTimeSeenLeft == 0) ? velMaxR * 0.4 : -velMaxL * 0.4;  // Gira pra direita
    (enemyLastTimeSeenLeft == 0) ? Serial.print("PROCURANDO ESQ \t\t") : Serial.print("PROCURANDO DIR \t\t");
  }
}

void setup() {
  // Inicia a Dory
  Serial.begin(115200);

  MotorsHBridgeDRV8833Init();
  Serial.println("Motores ON  ");

  IRJudgeControllerSensorInit();
  Serial.println("Controle Remoto ON ");

  distanceSensorsInit();
  Serial.println("Sensores Distancia ON  ");

  Serial.println("Setup Terminado!!!");
  delay(500);
}

void loop() {
  // Checa o sensor
  checkSensorIR();              // De acordo com o botão clicado, muda o mode
  readDistanceSensorsValues();  // Atualiza os valores da distância

  // Roda a programação de acordo com os casos do sensor de IR
  if (isRunning) {
    simpleStrategy();
  }

  sendPWMToMotors();  // Manda as velocidades para a ponte H

  distanceSensorsPrint();
  motorsPrintVel();
}

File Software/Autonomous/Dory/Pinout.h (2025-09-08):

//Board esp32 1.0.4
#ifndef LED_BUILTIN
#define LED_BUILTIN 2
#endif


// Motores da Esquerda e da direita
#define MOTOR_RIGHT_IN1_PIN 14 // Também é o pino da ESC1
#define MOTOR_RIGHT_IN2_PIN 27 // Também é o pino da ESC2
#define MOTOR_LEFT_IN1_PIN 26
#define MOTOR_LEFT_IN2_PIN 25

// Sensores de distância
#define DIST_SENSOR_SHARP_LEFT_PIN 34
#define DIST_SENSOR_SHARP_RIGHT_PIN 35

// SCL, SDA para a comunicação I2C
// Como usamos os pinos padrões da I2C, a biblioteca Wire.h cuida
// disso automaticamente para nós. Então essas variáveis não seriam necessárias.
#define SCL_PIN 22
#define SDA_PIN 21

// Define o pino XSHUT do sensor de distância VL53L0X
// Quando LOW, esse pino desliga o sensor e permite o endereçamento dos outros
int VL53LOX_XSHUT_LIST_PINS[3] = {17, 16, 4};

// Pino que retorna o valor recebido pelo controle do Juiz
#define JUDGE_CONTROLLER_PIN 39

// Pinos do de Interrupt do MPU e Motion do Mouse
#define INT_MPU 32
#define MOT_MOUSE 13

// Pino do divisor de tensao
#define DDT 33

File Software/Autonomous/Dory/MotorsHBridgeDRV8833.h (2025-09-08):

// Lista com os pinos de entrada dos motores
const int motorsInputPins[4] = { MOTOR_RIGHT_IN1_PIN, MOTOR_RIGHT_IN2_PIN, MOTOR_LEFT_IN1_PIN, MOTOR_LEFT_IN2_PIN };

// Estabelecendo os canais PWM que serão utilizados
// Como os motores estão espelhados, para girar na mesma direção,
// precisamos fazer a ordem 1 0 2 3, ao invés de 0 1 2 3
// vinculando assim o IN1 com o canal IN2 e o IN2 com o canal IN1
const int chRightIN1 = 1;  // Canal PWM 1 que irá ser vinculado ao pino MOTOR_RIGHT_IN2_PIN da ponte H
const int chRightIN2 = 0;  // Canal PWM 0 que irá ser vinculado ao pino MOTOR_RIGHT_IN1_PIN da ponte H
const int chLeftIN1 = 2;   // Canal PWM 2 que irá ser vinculado ao pino MOTOR_LEFT_IN1_PIN da ponte H
const int chLeftIN2 = 3;   // Canal PWM 3 que irá ser vinculado ao pino MOTOR_LEFT_IN2_PIN da ponte H

// Configurando o PWM
const int freq = 50;                           // Frequência do PWM, definida em 50Hz
const int resolution = 12;                     // Resolução do PWM, 12 bits, de 0 a 4095.
const int totalBits = pow(2, resolution) - 1;  // Magnitude máxima que o motor recebe e interpreta como 100% da velocidade

// Variáveis responsáveis pela velocidade
double velMotorR = 0;        // Vel direita, vai de [-100, 100]
double velMotorL = 0;        // Vel esquerda, vai de [-100, 100]
double velMotorRMapped = 0;  // Vel direita, vai de [-totalBits, totalBits]
double velMotorLMapped = 0;  // Vel esquerda, vai de [-totalBits, totalBits]

void MotorsHBridgeDRV8833Init() {
  for (int i = 0; i < 4; i++) {
    pinMode(motorsInputPins[i], OUTPUT);   // Fazemos os pinos MOTOR_RIGHT_IN1_PIN, MOTOR_RIGHT_IN2_PIN, MOTOR_LEFT_IN1_PIN e MOTOR_LEFT_IN2_PIN serem OUTPUTs
    ledcSetup(i, freq, resolution);        // Atribui a todos os canais i (= 0, 1, 2, 3) a frequencia de 50Hz com resolucao de 12bits.
    ledcAttachPin(motorsInputPins[i], i);  // Associamos os pinos MOTOR_RIGHT_IN1_PIN, MOTOR_RIGHT_IN2_PIN, MOTOR_LEFT_IN1_PIN e MOTOR_LEFT_IN2_PIN aos canais i (= 0, 1, 2, 3) respectivamente.

    // Na placa modular usamos o pino 14, que inicia como HIGH,
    // A roda então ficaria rodando durante o setup()
    // Essa linha garante que a roda pare assim que possível
    ledcWrite(i, 0);
  }
}

void sendPWMToMotors() {
  // IN1 --> Horário, Positivo -------- IN2 --> Anti-horário, Negativo
  // A velocidade zero é um caso especial. Então em casos gerais:
  // Quando estamos indo do Horário pro Anti-Horário (IN1 --> IN2), o 0 deve ser do canal IN1
  // Quando estamos indo do Anti-Horário pro Horário (IN2 --> IN1), o 0 deve ser do canal IN2

  // Precisa passar pelo 0 sempre que muda de direção. O valor Mapped ainda tem guardado a velocidade do último loop nele.
  if (velMotorR > 0 != velMotorRMapped >= 0) ledcWrite((velMotorRMapped > 0) ? chRightIN1 : chRightIN2, 0);
  if (velMotorL > 0 != velMotorLMapped >= 0) ledcWrite((velMotorLMapped > 0) ? chLeftIN1 : chLeftIN2, 0);

  //Mapeia o valor da escala [-100, 100] para a escala do PWM
  velMotorRMapped = map(velMotorR, -100, 100, -totalBits, totalBits);
  velMotorLMapped = map(velMotorL, -100, 100, -totalBits, totalBits);

  //Envia para o motor o sinal PWM
  ledcWrite((velMotorR > 0) ? chRightIN1 : chRightIN2, abs(velMotorRMapped));
  ledcWrite((velMotorL > 0) ? chLeftIN1 : chLeftIN2, abs(velMotorLMapped));
}

void motorsPrintVel() {
  Serial.println("Esquerda: " + (String)velMotorL + "\tDireita: " + (String)velMotorR);
}

void printMotorsSpeed() {
  Serial.print("VelL: " + (String)velMotorL + "   VelR: " + (String)velMotorR);
  Serial.print("\t");
}

String printInternetMotorsSpeed() {
  return "  VelL: " + (String) velMotorL + "   VelR: " + (String) velMotorR;
}

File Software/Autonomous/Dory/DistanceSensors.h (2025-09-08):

// ---------------------------------------------//
// --------VL53L0X CONSTANTS DECLARATION--------//
// ---------------------------------------------//


#include <VL53L0X.h>  // Sensores de distância, Pololu 1.3.1
#include <Wire.h>     // Auxiliar dos sensores

VL53L0X sensorL;  // Sensor da esquerda
VL53L0X sensorC;  // Sensor do centro
VL53L0X sensorR;  // Sensor da direita

VL53L0X* sensorsList[3] = { &sensorL, &sensorC, &sensorR };  // Lista de ponteiros com os sensores

uint8_t sensorsAddresses[3] = { 0x1, 0x2, 0x3 };  // Endereços pro I2C

int distL;  // Valor lido pelo sensor da esquerda
int distC;  // Valor lido pelo sensor da frente
int distR;  // Valor lido pelo sensor da direita

// ---------------------------------------------//
// -----SHARP 0A41SK0F CONSTANTS DECLARATION----//
// ---------------------------------------------//

#define DISTANCE_ARRAY_LENGHT 20  // Tamanho da lista utilizada para armazenar as medidas do Sharp

// Estabelece a leituras das distâncias SHARP
int distanceCenterLeftList[DISTANCE_ARRAY_LENGHT] = { 0 }; // Lista das distâncias lidas da esquerda
int distanceCenterRightList[DISTANCE_ARRAY_LENGHT] = { 0 }; // Lista das distâncias lidas da direita
int distanceCenterLeft = 0; 
int distanceCenterRight = 0;
int minimumDistanceSharp = 50;


// ---------------------------------------------//
// --------- SHARP 0A41SK0F FUNCTIONS ----------//
// ---------------------------------------------//


void distanceSensors0A41SK0FInit() {
  pinMode(DIST_SENSOR_SHARP_LEFT_PIN, INPUT);
  pinMode(DIST_SENSOR_SHARP_RIGHT_PIN, INPUT);
}

// Leitura da lista de distância
int returnAverageValue(int list[DISTANCE_ARRAY_LENGHT]) {
  int sum = 0;
  for (int i = 0; i < DISTANCE_ARRAY_LENGHT; i++) sum += list[i];
  return sum / DISTANCE_ARRAY_LENGHT; // Média da lista de distância
}

// Atualiza as distâncias reconhecidas pelo sensor
void updateAvgDistanceLists(int centerLeftAnalogRead, int centerRightAnalogRead) {
  for (int i = 0; i < (DISTANCE_ARRAY_LENGHT - 1); i++) distanceCenterLeftList[i] = distanceCenterLeftList[i + 1];
  distanceCenterLeftList[DISTANCE_ARRAY_LENGHT - 1] = centerLeftAnalogRead; // Atualiza com o dado mais novo lido e retira a leitura mais antiga (sensor da esquerda)
  for (int i = 0; i < (DISTANCE_ARRAY_LENGHT - 1); i++) distanceCenterRightList[i] = distanceCenterRightList[i + 1];
  distanceCenterRightList[DISTANCE_ARRAY_LENGHT - 1] = centerRightAnalogRead; // Atualiza com o dado mais novo lido e retira a leitura mais antiga (sensor da direita)
}

void readDistanceSensors0A41SK0FValues() {
  updateAvgDistanceLists(analogRead(DIST_SENSOR_SHARP_LEFT_PIN), analogRead(DIST_SENSOR_SHARP_RIGHT_PIN));
  distanceCenterLeft = returnAverageValue(distanceCenterLeftList);
  distanceCenterRight = returnAverageValue(distanceCenterRightList);
}


// ---------------------------------------------//
// ------------- VL53L0X FUNCTIONS -------------//
// ---------------------------------------------//


void distanceSensorVL53L0XInit() {

  Wire.begin();  // Inicia o I2C
  Wire.setClock(400000); //TODO: iniciar o Wire em uma funcao separada no setup do codigo

  // Desliga todos os sensores
  for (int i = 0; i < 3; i++) {
    pinMode(VL53LOX_XSHUT_LIST_PINS[i], OUTPUT);
    digitalWrite(VL53LOX_XSHUT_LIST_PINS[i], LOW);
  }

  delay(10);

  //Endereça todos os sensores
  for (int i = 0; i < 3; i++) {
    pinMode(VL53LOX_XSHUT_LIST_PINS[i], INPUT); // XSHUT volta pra HIGH
    sensorsList[i]->init(); // Inicia o sensor usando a função da lib
    sensorsList[i]->setAddress(sensorsAddresses[i]); // Endereça o sensor
    sensorsList[i]->setTimeout(100); // Tempo que pode ficar sem responder
    sensorsList[i]->startContinuous(); // Modo contínuo, ↓ Precisão ↑ Velocidade
    delay(10);
  }
}

void readDistanceSensorsVL53L0XValues() {
  // Armazena os valores lidos nos sensores
  distL = sensorL.readRangeContinuousMillimeters();
  //distC = sensorC.readRangeContinuousMillimeters(); //Atualmente, não usamos
  distR = sensorR.readRangeContinuousMillimeters();
}


// ---------------------------------------------//
// ------------- GENERAL FUNCTIONS -------------//
// ---------------------------------------------//


void distanceSensorsInit() {
  distanceSensors0A41SK0FInit();
  distanceSensorVL53L0XInit();
}

// Atualiza com as novas leituras e retorna a variável para ocorrer o que é esperado dado a programação
void readDistanceSensorsValues() {
  readDistanceSensors0A41SK0FValues();
  readDistanceSensorsVL53L0XValues();
}

void distanceSensorsPrint() {
  Serial.print(+ "L: " + (String)distL
            + "\tC-L: " + (String)distanceCenterLeft
            + "\tC-R: " + (String)distanceCenterRight
            + "\tR: " + (String)distR);
}

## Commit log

2023-03-18 add: Electronics and Mechanics files
    [Base_Support.step, CONTROLE.sch, DORY-PLACA.kicad_pcb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]
2023-03-26 fix: organizing Electronics and Mechanical folders
    [Base_Support.step, CONTROLE.sch, DORY-PLACA.kicad_pcb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]
2023-03-26 fix: organizing Software folder
    [Dory.ino]
2023-12-31 feat: start ESP32 compatible code
2024-01-23 fix: change on Simple Strategy
    [DistanceSensors.h, Dory.ino]
2024-01-30 fix: motors errors
2024-02-23 fix: motors corrections
2024-02-28 fix: delay on motors
    [Dory.ino]
2024-04-20 chore: update electronics files
    [CONTROLE.sch, DORY-PLACA.kicad_pcb, DORY-PLACA.sch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]
2024-05-15 chore: update Mechanics files
    [Base_Support.step, Chassis.stl, Dory_Hub v1.stl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]
2024-06-15 add: Dory's Schematic
    [Dory_electronics.kicad_sch]
2024-06-15 chore[Electronics]: add h bridge and IR
    [Dory_electronics.kicad_sch]
2024-06-20 fix: organize Electronics folder
    [Dory_electronics.kicad_pcb, Dory_electronics.kicad_sch]
2024-06-20 chore: organize schematic and add gitignore
    [Dory_electronics.kicad_sch]
2024-06-21 feat: add VL530X
    [Dory_electronics.kicad_pcb, Dory_electronics.kicad_sch, esp32_devkit_v1_doit.step]
2024-06-29 fix(Electronics): remove center vl53l0x from sch
    [Dory_electronics.kicad_sch]
2024-07-02 chore: revision of the PCB
    [Dory_electronics.kicad_sch]
2024-07-17 chore: update Electronics
    [Dory_electronics.kicad_sch]
2024-08-31 chore: add footprints to schematic
    [Dory_electronics.kicad_sch]
2024-09-03 chore(Electronics): organize and finish schematic
    [Dory_electronics.kicad_pcb, Dory_electronics.kicad_sch]
2024-09-07 chore: update schematic and PCB
    [Dory_electronics.kicad_pcb, Dory_electronics.kicad_sch]
2024-09-13 chore: redo paths to homemade pcb
    [Dory_electronics.kicad_pcb, Dory_electronics.kicad_sch]
2024-09-14 chore: change .step to be above pcb
2024-09-14 chore: update esp32 lib sym and footprint
    [Dory_electronics.kicad_pcb, Dory_electronics.kicad_sch]
2024-09-15 chore: Add/Update 3D models on PCB
    [Dory_electronics.kicad_pcb, Dory_electronics.kicad_sch]
2024-09-28 chore: update PCB and create BOM file
    [Dory_electronics.csv, Dory_electronics.kicad_pcb, Dory_electronics.kicad_sch]
2024-10-05 chore: add VL53L0X to code
    [BOTTOM-Suporte-Dory.stl, TOP-Suporte-Dory.stl]
2024-10-10 fix: fix IR judge controller buttons
    [IRJudgeControllerVS1838B.h]
2025-09-08 docs(Mechanics): add drawings
    [Dory_Main_Body Atualizado v5.stl, Suporte sensores inclinado.stl, Suporte sensores reto.stl]
2025-09-08 docs(Electronics): add modular PCB
    [Dory_electronics.csv, Dory_electronics.kicad_pcb, Dory_electronics.kicad_sch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]
